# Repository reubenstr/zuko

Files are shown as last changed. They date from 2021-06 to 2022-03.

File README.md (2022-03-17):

# Zuko - A quadruped robot dog!

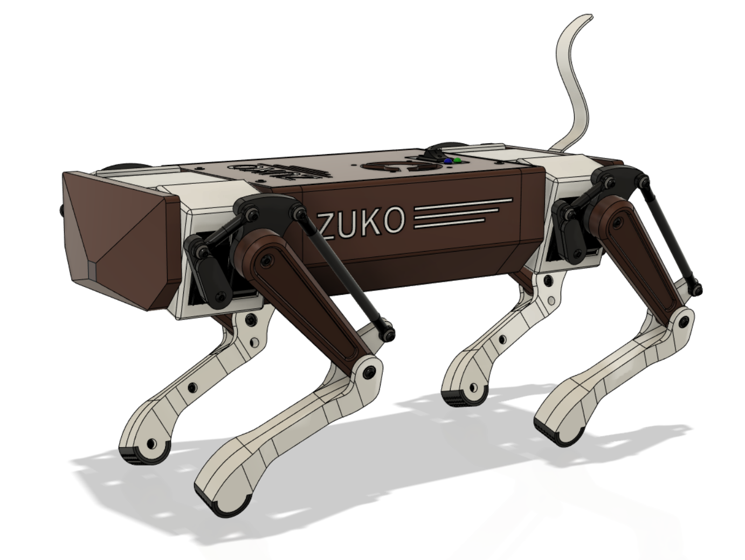
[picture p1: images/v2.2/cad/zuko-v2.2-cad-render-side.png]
 | 
------------ | 
Frame v2.2 CAD design. |

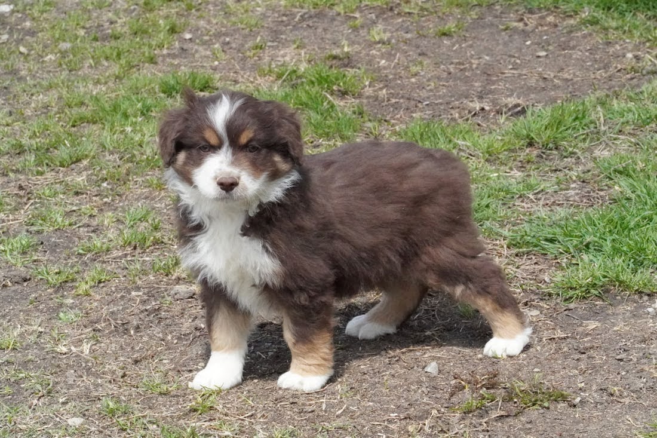
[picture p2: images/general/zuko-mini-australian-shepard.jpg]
 | 
------------ | 
Zuko himself! |

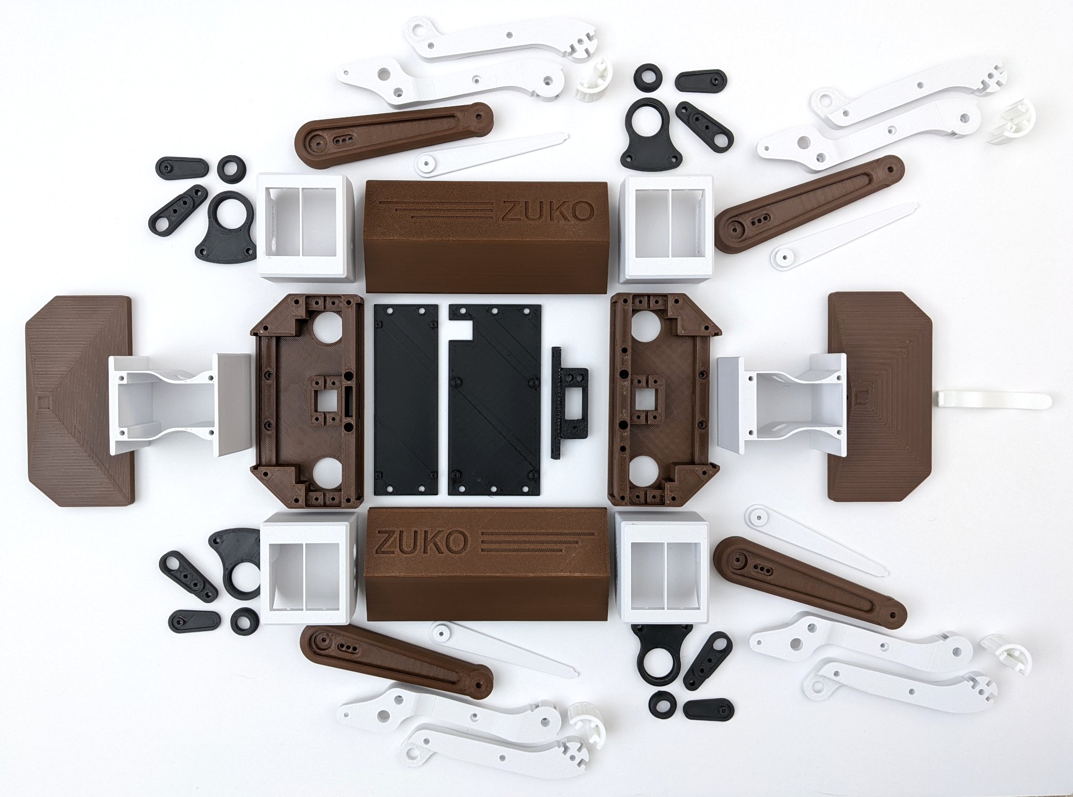
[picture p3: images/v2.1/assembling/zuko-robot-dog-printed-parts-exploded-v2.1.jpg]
 | 
------------ | 
Frame v2.1 parts printed. |

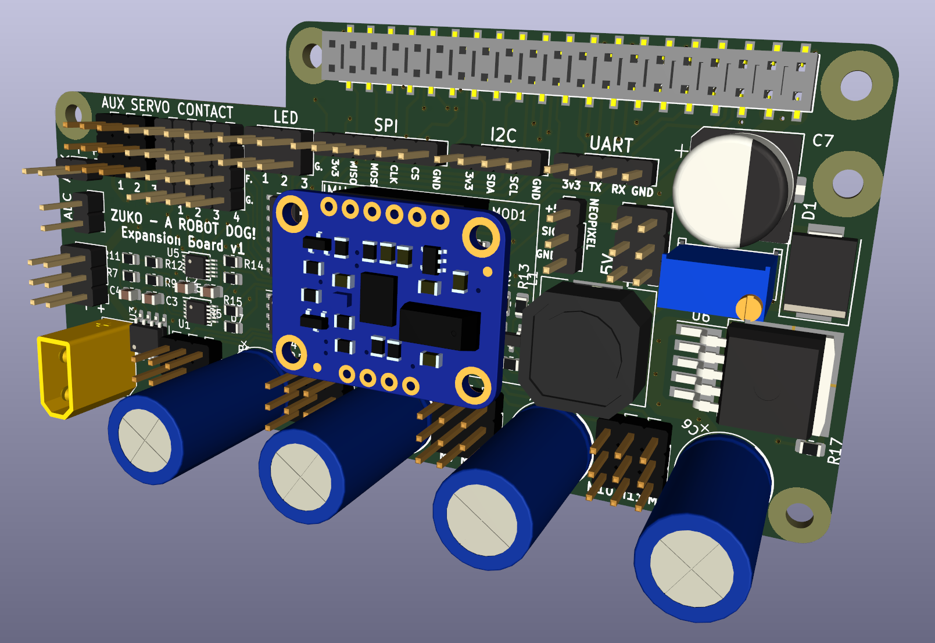
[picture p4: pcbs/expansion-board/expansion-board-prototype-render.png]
 | 
------------ | 
Expansion board v1 for direct RPi inteface. |

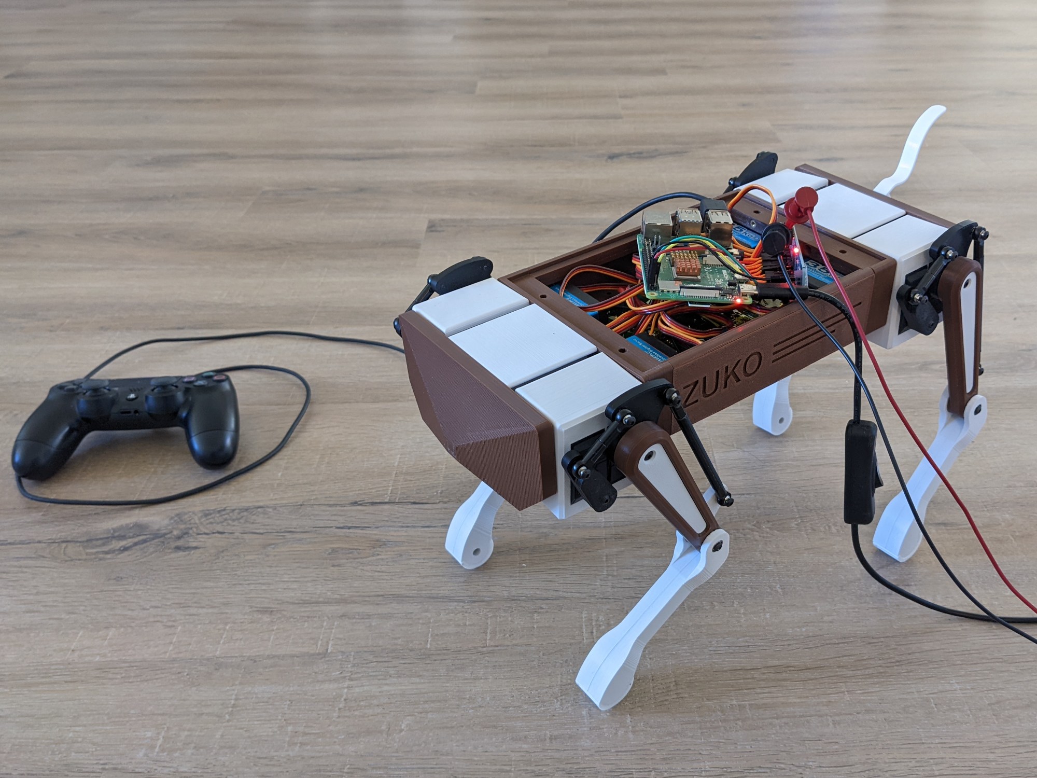
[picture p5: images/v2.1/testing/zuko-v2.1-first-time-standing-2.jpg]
 | 
------------ | 
Frame v2.1 first time standing. |

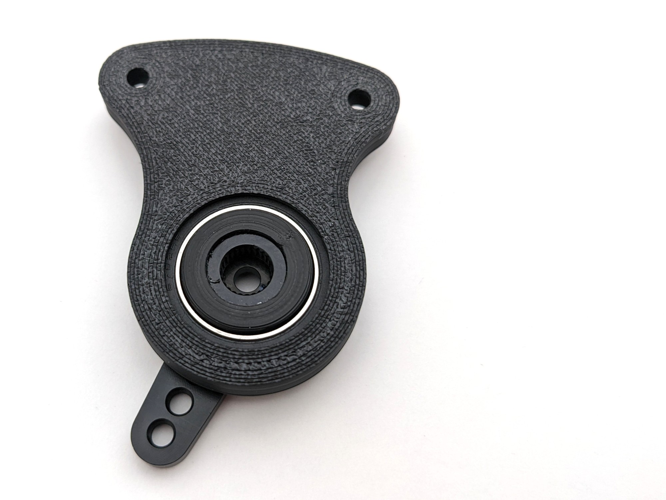
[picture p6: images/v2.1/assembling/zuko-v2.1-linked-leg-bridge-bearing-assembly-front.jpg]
 | 
------------ | 
Frame v2.1 upper leg's servo horn, linked leg bridge, and bridge bearing press fit together. |

Watch the video (https://youtu.be/D2snHtP22o0) | 
------------ | 
Video: frame v2.1 first tests |

Watch the video (https://youtu.be/J1g2Bx3SKjw) | 
------------ | 
Video: Sydney meets Zuko |

### Status

**Development.**  

**V2.2 Frame is being tested and is nearly ready for replication**

### General

Zuko uses the ROS2 framework for communication, launching, and 3rd party addons. Zuko uses a Rasberry Pi 4 with a custom expansion board for motor and peripheral control via a Playstation 4 controller.

### Current Major Tasks 

- Complete ROS2 tasks - in progress
- Fab/test expansion-board PCB
- Update BOM
- Create PCB BOM
- Upload STL's
- Create print time/weight sheet
- Create how to documentation for end user

### ROS2 Workspace 

ROS2 source code is contained the quad_ws directory.

### My contributions
- Frame redesign using larger servos, providing more space for electronics, rework of the leg/hip system, and addition of aesthetic features (tail, etc).
- Migration of source code from ROS1 to ROS2 (Robot Operating System) frameworks.
- Inverse kinematics for a linked leg system for OpenQuadruped / Spot Mini Mini based quadrupeds.
- Parameterized duplicated hard-coded values.
- Created servo calibration script for quicker calibration and servo support.- 
- A more feature rich motor and peripheral expansion board using a Teensy 4.0 supporting aux servos, foot sensors, NeoPixls, etc.
- 8x 18650 user accessable battery holder with onboard BMS (battery management system). 
  
### Credits
- Simulation, kinematics, bezier curves, and machine learning are largely based on the work from Spot Mini Mini: https://github.com/OpenQuadruped/spot_mini_mini 
- Spot Mini Mini is based on SpotMicroAI: https://spotmicroai.readthedocs.io/en/latest/
- Frame and leg linkage design inspired by Baris Alp's Kangel robot dog: https://grabcad.com/library/diy-quadruped-robot-1

### Communities
- SpotMicroAI Discord: https://discord.gg/m5fsENhT
- Quadrupedalism: https://quadrupedalism.com/

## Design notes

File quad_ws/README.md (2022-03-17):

# rpi_quad_ws
RPi 4 ROS2 workspace Zuko.

### Status

Development.

### Immediate To Do

- Update motor limits
- Finish URDF: add final STLs, add weights
- Add discovery to launch for remote simulation from RPi
- Update walking parameters
- Code in IMU, V/I sense, LEDs
- Pythonize code (clean up code)
- (clean model.py, urdf pathing)

### Long Term To Do

- Reconnect machine learning for better terrain navigation
- Update URDF for Gazebo
- Add speakers for barks
- Add camera for CV

### Notes

View documentation in the dev-notes folder

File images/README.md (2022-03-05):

# Zuko - images

When assembling check the latest CAD model as some pictures may show parts from past versions. 

Previous version pictures may be applicable to the current version, explore everything!

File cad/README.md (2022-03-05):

# Frame Versions

Select the latest version if you intend to make or redesign your own robot dog.

See the STL folder for assembly tools.

### v2.2 Change Log

	Removed TPU feet.
		Reduces filament types and lowers cost.
	Added EVA tape feet.
		Inceases grip.
	Lower legs redesigend to accommodate EVA tape feet.
	Added EVA tape feet glueing jig.

### v2.1 Change Log

	25t spline to gear adapters replaced with common servo horn.
		Increases part accessibility and to reduce cost. Suggested by SnowGliderr.
	Upper leg, lower leg servo horn, and hips redesigned to accept new servo horn.
	Frame bridge added top/bottom flair outs for aesthetics.
	Single unit electronics mounting plate for expansion board mounting direct to RPi4.
	Minor tweaks applied during assembly.
	
### v2.0 Change Log

	Replaced hip drive belts with direct drive by relocating hip motors into the electronics bay.
	Updated front and back center frames to support direct drive.
	Lengthened frame sides to accommodate space requirements for direct drive.
	Revised frame bridge from two peices into one to accommodate the removal of the hip servos. 
	Added ring bearing to upper leg and leg linkage bridge.
	Converted upper leg into two components, upper leg and gear interface, to accommodate the ring bearing's press fit joint.
	Revised hip joint pulley to accommodate direct drive.
	Added more support to the hip pulley connection area.
	Added more material support around lower leg linkage connection point.
	Revised lower leg to include a flair at the paw area.
	Removed brass insert requirement from hips, now using course threaded screws.
	Relocated power switch with stury direct frame connection.

	Results: 
		Pros:
			Fewer 3D printed parts, filament types, and hardware.
			No friction bearings.
			No stretchy hip angles.
			No leg assembly bridge wobble.
		Cons:			
			5mm longer frame resulting electronics bay space reduction (but electronics able to be housed in frame bridge)

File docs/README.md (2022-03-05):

# Docs

Documentation is currently being updated to reflect frame v2.2, the new RPi expansion board, and the updated ROS2 workspace quad_ws.

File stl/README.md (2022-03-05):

# STL

The main assembly archive located in the CAD folder will always contain the most up to date STL's.

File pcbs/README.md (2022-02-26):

# PCBs
 
PCBs created in KiCad 6.0

https://www.kicad.org/download/

All works in progress, PCBs on the way for testing, not for production.

There are currently two paths for controlling the servos and peripherals:

1) Expansion board: RPi 4 direct connect using PWM and ADC controllers of I2C
	
2) Motor Controller: Teensy is responsible for PWM and ADC at the expense of complex micro-ros.

### Expansion Board

RPi expansion board to control servo motors and other peripherals without using a microcontroller.

Fabrication specifications: 4 layer, 1oz (2oz preferred and may be required, testing still in progress).

### Battery Board

Mounts 8x 18650 LiPo batteries and 4x HY2120 (or similar) battery managment systems.

Fabrication specifications: 2 layer, 1oz (2oz preferred and may be required, testing still in progress).

### Motor Controller

Controls 12 motion RC servos using a Teensy 4.0 microcontroller. 

Connects to and powers RPi.

Requires external DC-DC converter to supply 5vDC to board and RPi.

Contains peripheral support for I2C IMU, touch down switches, LED, Neopixel (ws2812b) led strips, current sense, voltage sense, auxillary RC servos, and extra I2C devices.

Fabrication specifications: 4 layer, 1oz (2oz preferred and may be required, testing still in progress).

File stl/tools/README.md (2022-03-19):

# STL

Tools used to aid in the assembly and fabrication of Zuko.

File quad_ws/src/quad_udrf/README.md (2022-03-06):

# quad_udrf

Work in progress.

Zuko's URDF package. Uses xacro to create UDRF files. Visualized in RVIZ.

Launch UDRF in RVIZ:
	ros2 launch quad_urdf display.launch.py

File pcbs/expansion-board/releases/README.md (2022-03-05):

# Expansion Board Versions

v1.0: initial prototype for physical fabrication

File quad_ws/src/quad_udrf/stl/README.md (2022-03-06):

# stl
STL's are optimized for visualization and simulation with low vertice counts. Find 3D print ready STL's in the main project repository either from the archived CAD model or the STL folder.

To update STL's from main CAD model, export meshes with the following parameters (using Fusion 360):
	Format: STL (Binary)
	Unit Type: Meter
	Refinement: Low
	 
Use Fusion 360 to determine the STL's origin to perform joint offset calculations.

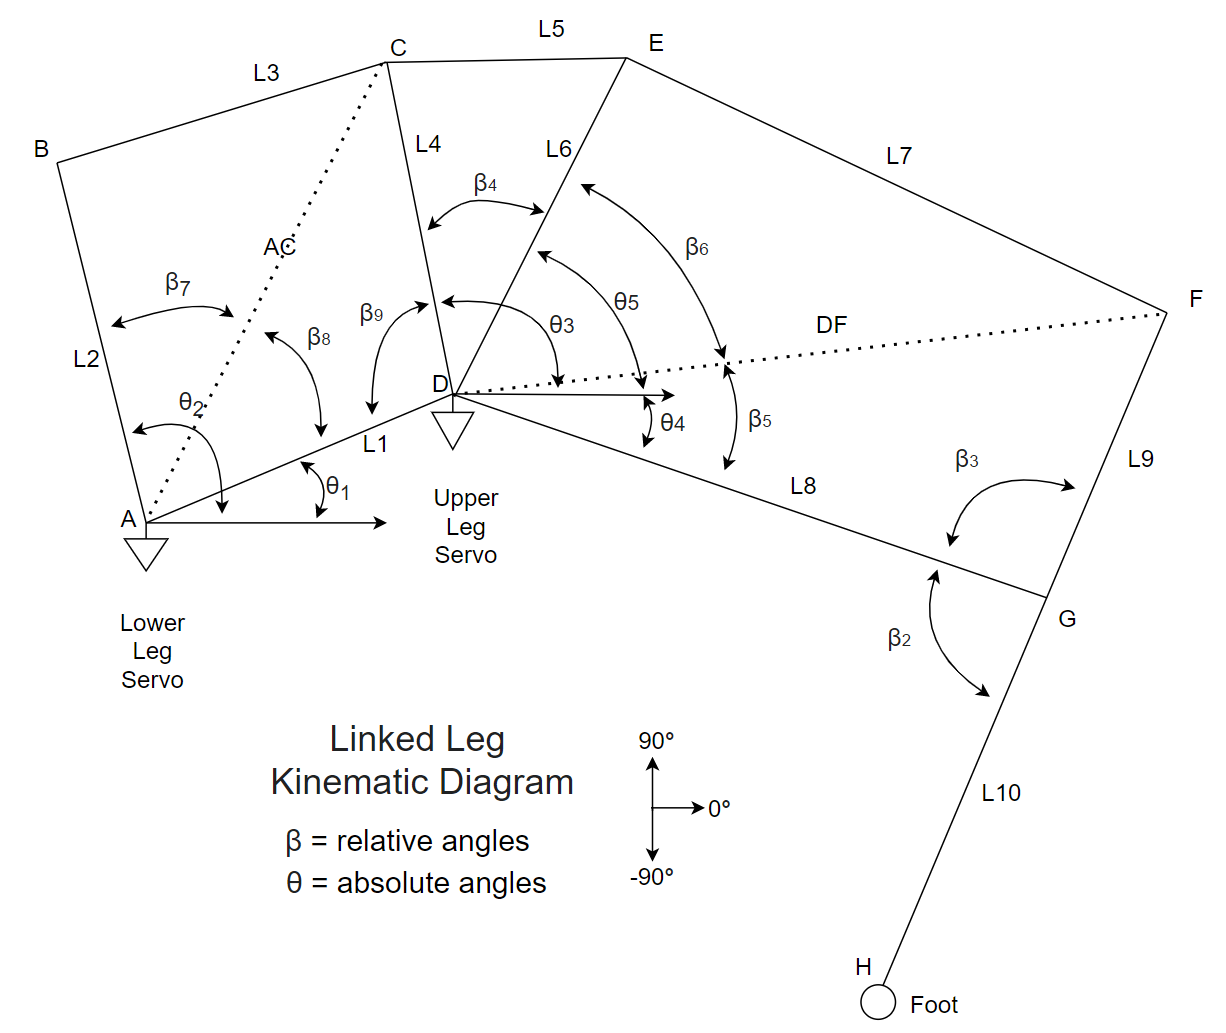
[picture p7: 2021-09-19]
diagrams/linked-leg-kinematic-dragram.png

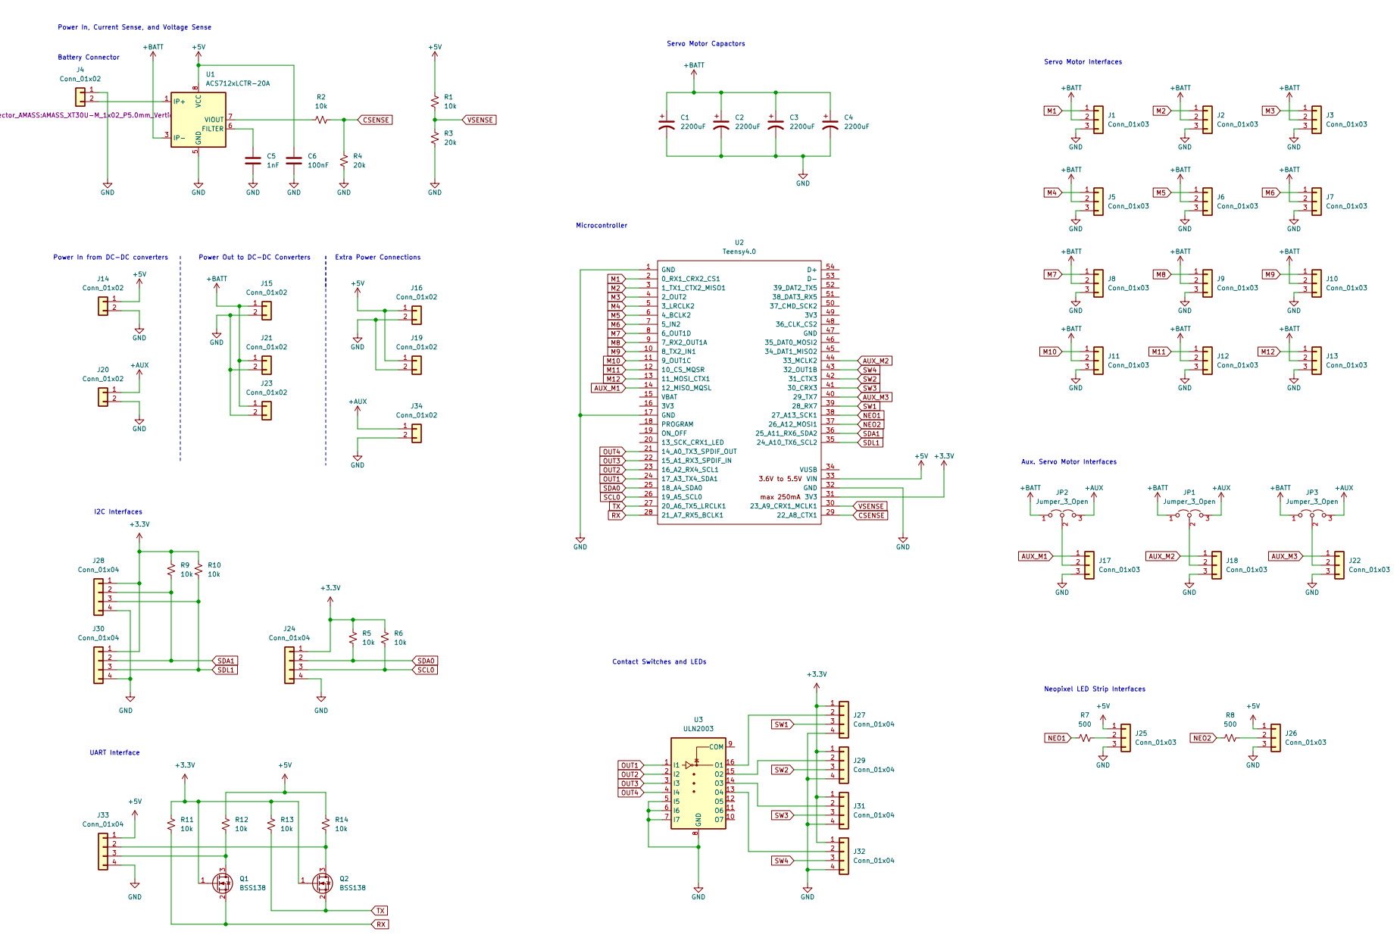
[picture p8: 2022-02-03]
pcbs/motor-controller/pcb-review-temp/pcb-schematic.png

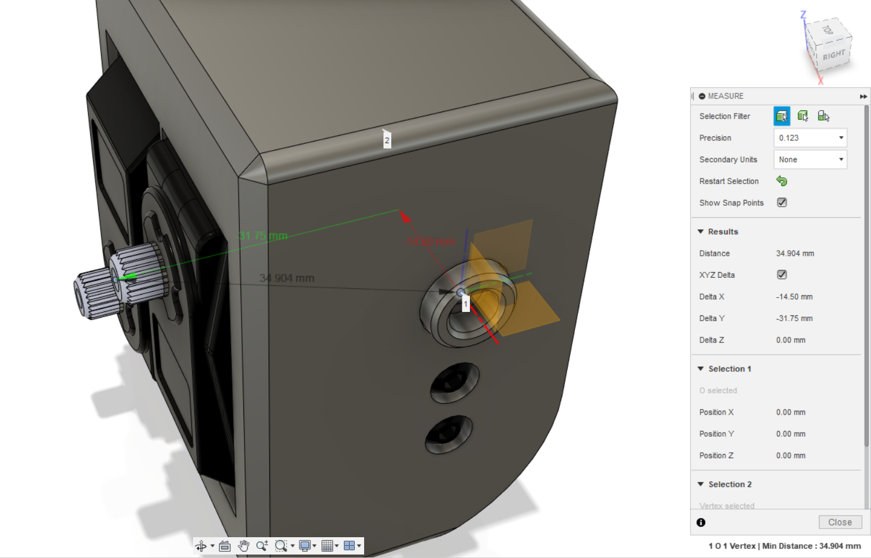
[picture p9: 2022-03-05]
images/general/zuko-showing-XYZ-delta-measuring-for-URDF-creation.png

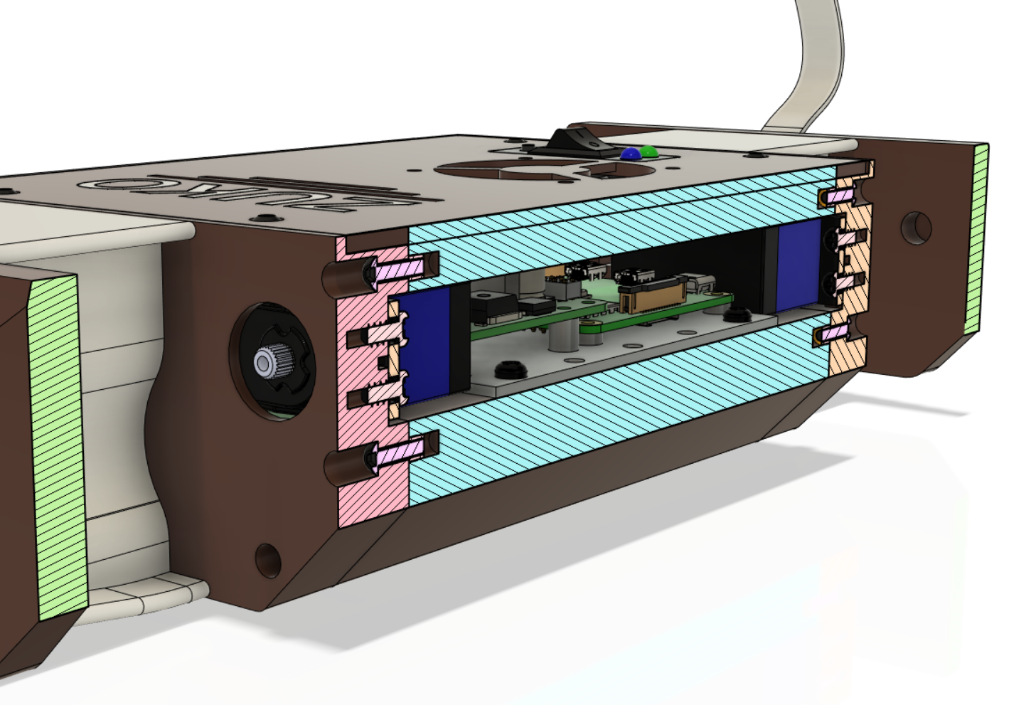
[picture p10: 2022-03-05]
images/v2.2/cad/zuko-v2.2-cad-render-side-cross-section.png

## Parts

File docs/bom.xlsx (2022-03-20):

Not fully updated for v2.2, check the CAD as it has most hardware
Links provided as examples.
Hardware | Qty. | Usages/Notes | Link1 | Link2
M3x3mm button head bolt | 8 | hip servo horn
M3x6mm button head bolt | 20 | PCB mounting plates, battery board, lower leg servo horn
M3x8mm button head bolt | 24 | combine lower legs, electronics bay cover, tail, hip bearing, power switch bracket, battery cover, lower leg bearing, front/back plate mount to sides
M3x12mm button head bolt | 32 | lower leg servo horn, lower leg tie rods
M3x16mm button head bolt | 8 | upper leg servo, lower leg feet
M3x65mm socket head bolt | 8 | center frames to bridge to face/butt
M4x8mm course thread self-tapping for plastic screw | 52
M2.3x6mm screw | 6 | RPi and expansion-board PCB mount
15mm x 21mm x 4mm, 6702-2RS bearing | 4 | Upper leg and lower leg bridge interface
8mm x 3mm x 4mm, 693ZZ bearing | 12 | hips, lower leg
M3x4.0mm, OD4.6mm threaded insert | TBD
M3x90mm threaded rod | 4 | lower leg tie rod
M3x16mm threaded rod | 4 | lower leg tie rod
M3 metal ball end tie rods | 16 |  | https://www.amazon.com/gp/product/B07FD4SMQJ
25T, 28.5mm length, 3x M3 holes servo horn | 12 |  | https://www.aliexpress.com/item/1005001513123335.html | https://www.amazon.com/gp/product/B09JLLWDW2
Mechatronics | Qty. | Usages/Notes | Link1 | Link2
35kg DSSERVO 180-degree servo | 12 | Testing on this specific servo is still being performed Many other high voltage high torque servos exists. | https://www.aliexpress.com/item/33010787343.html
Electronics | Qty. | Usages/Notes | Link1 | Link2
Rocker switch | 1
XT30 male | 1
XT30 Female | 1
Tactile switch | 1
5mm LED blue | 1
5mm LED red | 1
16AWG silicon multi-stranded
Heat shrink tubing
RPi 4
Rpi 4 expansion-board PCB |  |  | See git repository for expansion-board KiCAD project
Expansion-board components |  | TODO, check the schematic meanwhile | See git repository for expansion-board KiCAD project
Battery holder PCB | 1 | TODO, check the schematic meanwhile | See git repository for battery-holder KiCAD project
Li-ion lithium battery 18650 protection board | 4 |  | https://www.amazon.com/gp/product/B08CV2VS8G
18650 battery holder 4x cell capacity | 2 |  | https://www.amazon.com/gp/product/B07PZKKZY2
18650 battery | 8 | Use trusted retailer to buy quality batteries
Kapton tape (polyimide) |  | Covers battery board to protect against shorts | https://www.amazon.com/dp/B072Z92QZ2
18650 battery charger | 1
Playstation 4 wireless controller | 1 | Code modification required for other controllers | https://www.amazon.com/dp/B07VBBJ6KZ
Consumables | Qty. | Usages/Notes | Link1 | Link2
ABS 1.75mm filament – primary color | 1 | eSun Brown ABS – excellent filament | https://www.amazon.com/gp/product/B00MVIPTH8
ABS 1.75mm filament – secondary color | 1 | eSun White ABS – might be replaced as white has low strength | https://www.amazon.com/gp/product/B00MV7T3TO
ABS 1.75mm filament – tertiary color | 1 | eSun black ABS– try to find the ABS+ version, prints well, looks good | https://www.amazon.com/dp/B00MV7T25E/
TPU 1.75 filament – optional | 1 | Overture white TPU – optional for a tail | https://www.amazon.com/gp/product/B07VGVW546
EVA tape – bike handle bar tape |  | Or other grip tape/foam, ~2.50mm thick | https://www.amazon.com/dp/B07RDHK8TW
Solder
Solder flux
Superglue (cyanoacrylate) |  | attaches EVA tape to foot | https://www.amazon.com/s?k=super+glue
Threadlocker blue |  | keeps tie rod bolts from backing out | https://www.amazon.com/s?k=blue+threadlocker

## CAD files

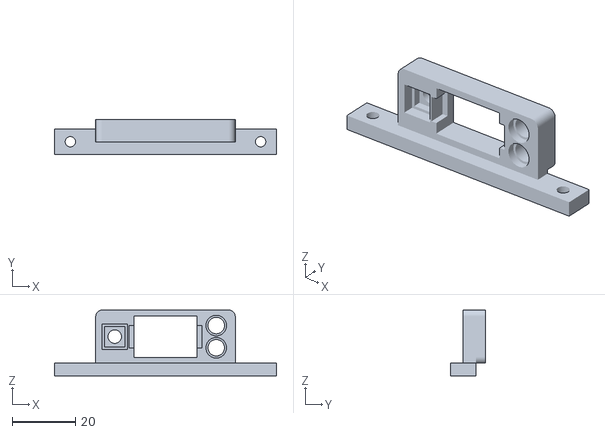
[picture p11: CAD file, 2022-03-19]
stl/v2.2/electronics - main switch mounting.stl
70.0 x 11.0 x 20.8

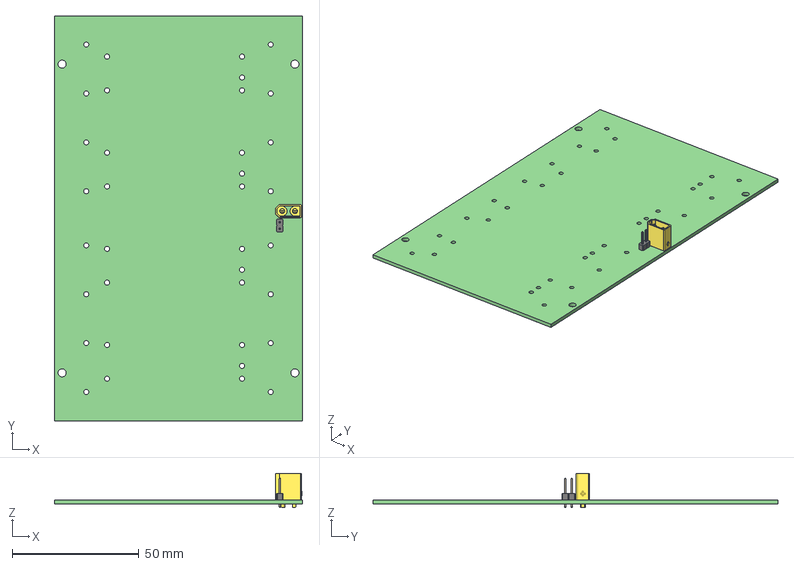
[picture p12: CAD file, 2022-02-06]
pcbs/battery-board/battery-board.step
98.0 x 160.0 x 13.5 mm
_autosave-battery-board PCB

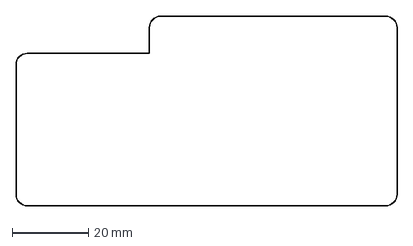
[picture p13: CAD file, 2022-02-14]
pcbs/expansion-board/expansion-board-pcb-outline.dxf
100.0 x 49.8 mm

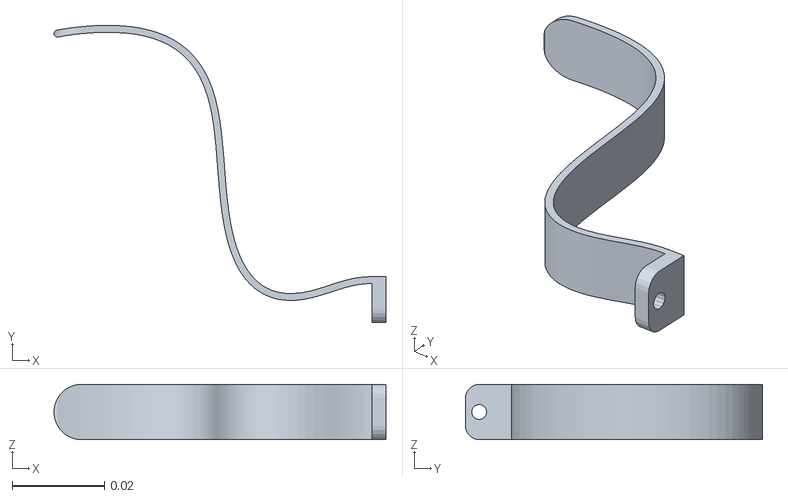
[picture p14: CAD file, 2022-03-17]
quad_ws/src/quad_simulation/quad_simulation/stl/tail.stl
0.072 x 0.0645 x 0.012

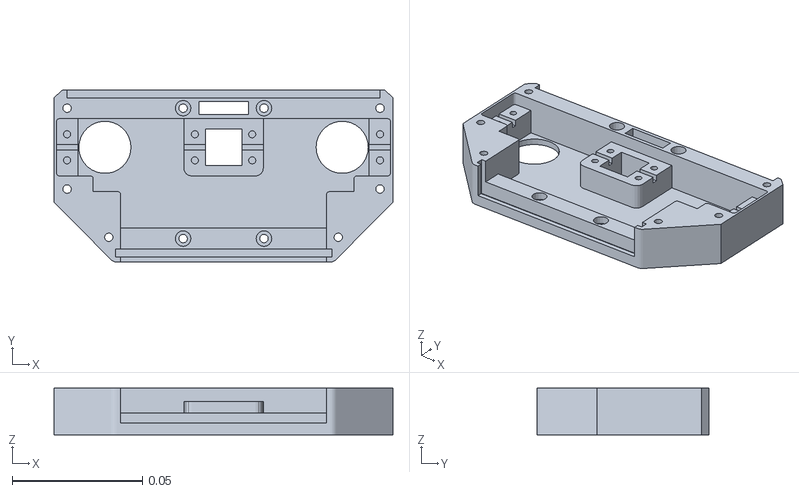
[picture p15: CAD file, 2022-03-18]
quad_ws/src/quad_udrf/stl/center_front.stl
0.13 x 0.066 x 0.018

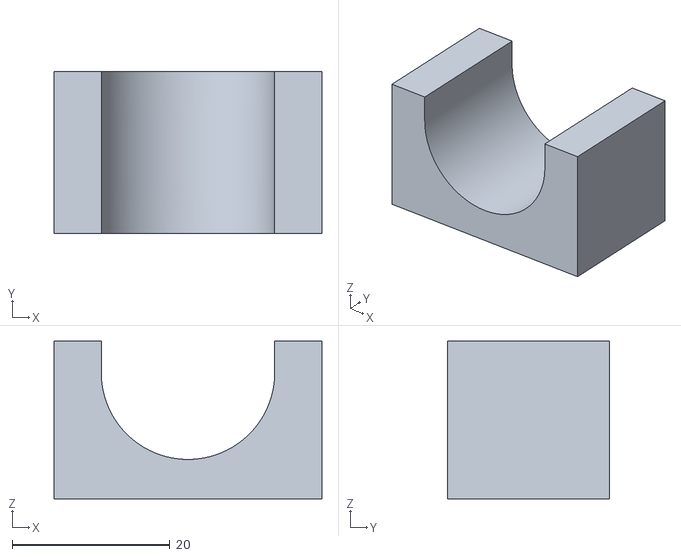
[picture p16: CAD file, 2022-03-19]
stl/tools/v2.2/tool - glue EVA tape to foot holder v2.stl
34.0 x 20.5 x 20.0

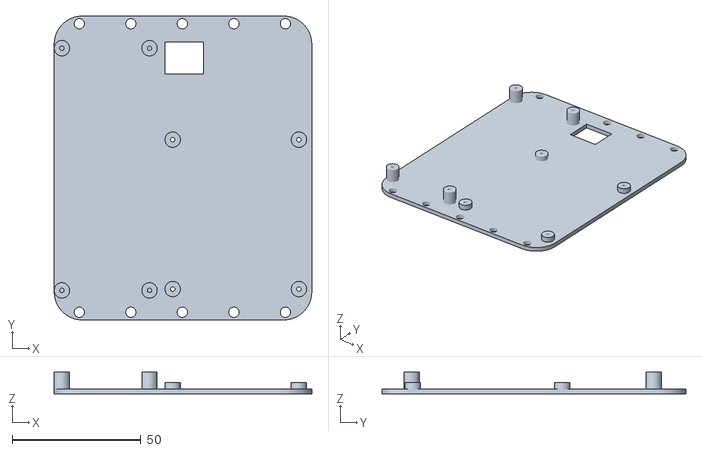
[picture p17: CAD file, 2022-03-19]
stl/v2.2/electronics - electronics mount.stl
100.0 x 118.0 x 8.50

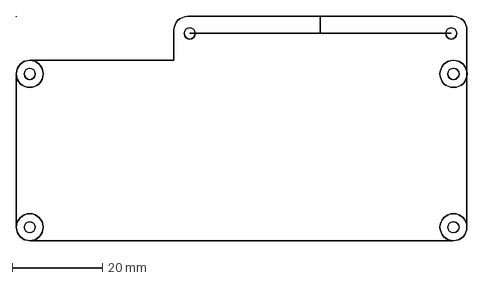
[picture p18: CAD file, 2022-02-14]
pcbs/expansion-board/expansion-board-user-guides.dxf
100.1 x 49.8 mm

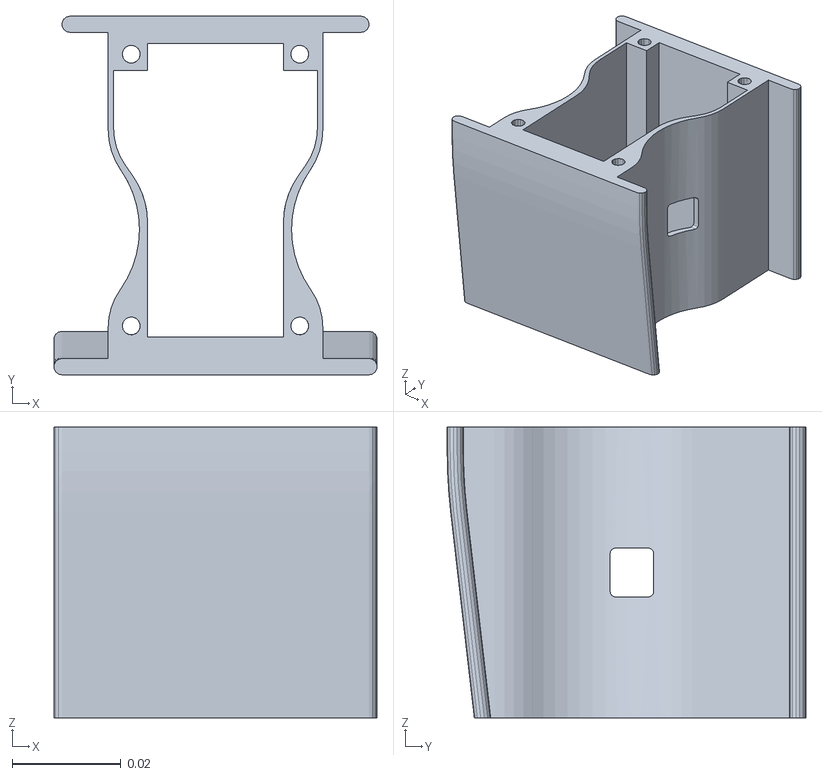
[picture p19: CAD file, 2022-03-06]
quad_ws/src/quad_simulation/quad_simulation/stl/bridge_front.stl
0.0594 x 0.066 x 0.0535

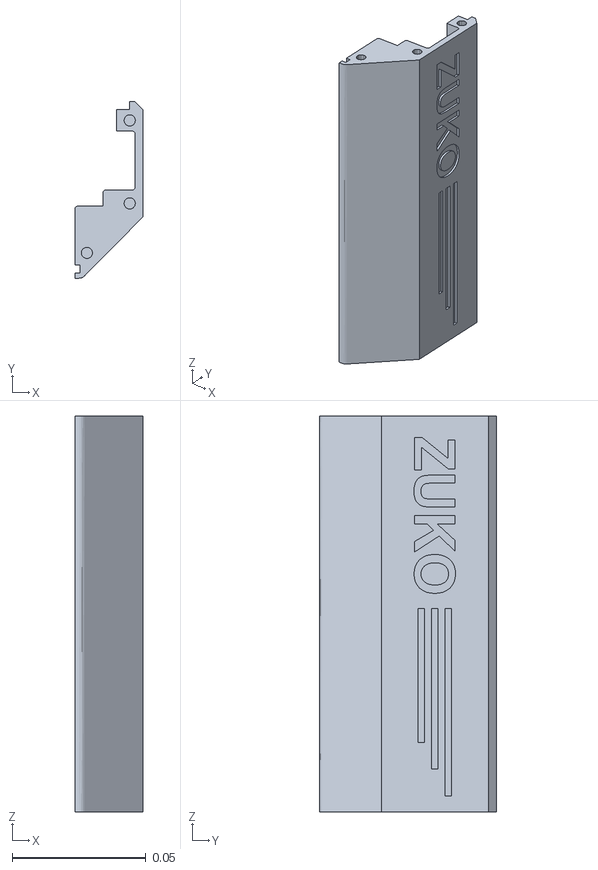
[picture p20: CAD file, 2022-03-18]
quad_ws/src/quad_udrf/stl/side_left.stl
0.0255 x 0.066 x 0.148

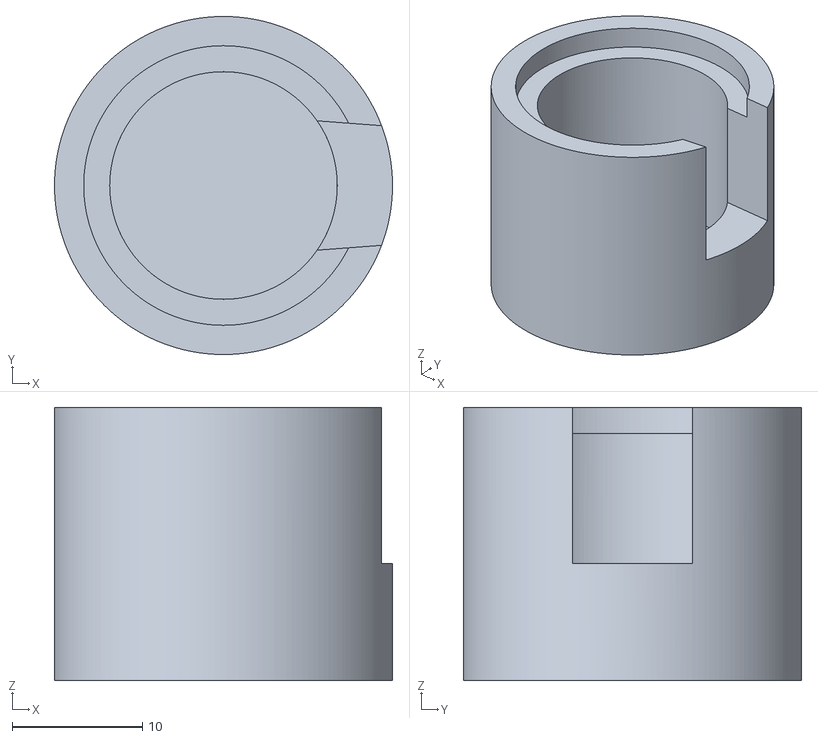
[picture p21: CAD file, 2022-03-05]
stl/tools/v2.2/tool - remove leg bearing from gear interface - hammer v8.stl
26.0 x 26.0 x 21.0

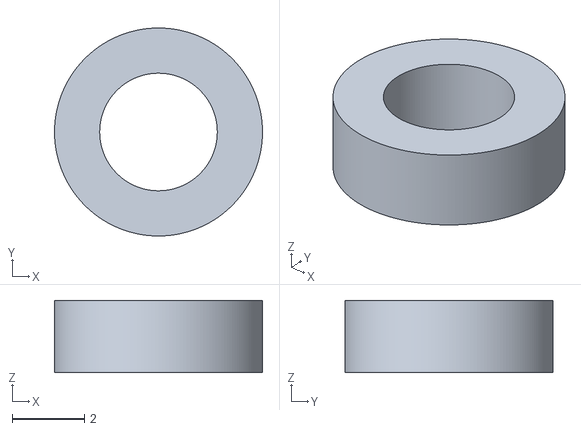
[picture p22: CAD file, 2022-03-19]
stl/v2.2/leg - upper - servo horn support ring.stl
5.75 x 5.75 x 2.00

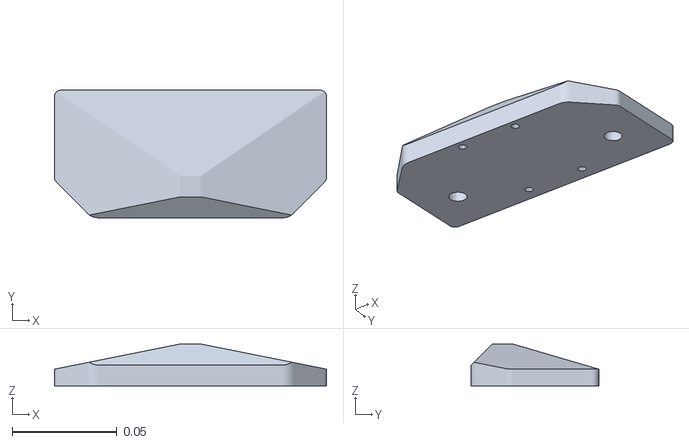
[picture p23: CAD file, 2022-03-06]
quad_ws/src/quad_simulation/quad_simulation/stl/face.stl
0.13 x 0.061 x 0.02

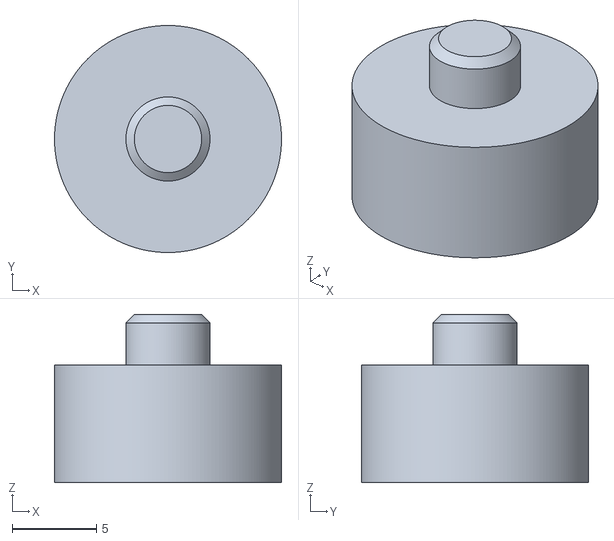
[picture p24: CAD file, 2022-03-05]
stl/tools/v2.2/tool - remove leg bearing from gear interface - base v6.stl
13.5 x 13.5 x 10.0

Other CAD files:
cad/v1.0/_ROBO_FRONT_FRAME.DXF
quad_ws/src/quad_udrf/stl/side_right.stl
stl/v2.2/electronics - battery cover.stl
quad_ws/src/quad_simulation/quad_simulation/stl/butt.stl
quad_ws/src/quad_simulation/quad_simulation/stl/bridge_back.stl
quad_ws/src/quad_simulation/quad_simulation/stl/center_back.stl
quad_ws/src/quad_simulation/quad_simulation/stl/center_front.stl
quad_ws/src/quad_simulation/quad_simulation/stl/hip_back.stl
quad_ws/src/quad_simulation/quad_simulation/stl/hip_front.stl
quad_ws/src/quad_simulation/quad_simulation/stl/lower_leg.stl
quad_ws/src/quad_simulation/quad_simulation/stl/side_left.stl
quad_ws/src/quad_simulation/quad_simulation/stl/side_right.stl
quad_ws/src/quad_simulation/quad_simulation/stl/upper_leg.stl
quad_ws/src/quad_udrf/stl/battery_cover.stl
quad_ws/src/quad_udrf/stl/bridge_back.stl
quad_ws/src/quad_udrf/stl/butt.stl
quad_ws/src/quad_udrf/stl/center_back.stl
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

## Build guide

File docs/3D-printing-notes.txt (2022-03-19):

3D PRINTING NOTES:

	Printing settings are tuned to the filament and printers used to create the orginal Zuko.
	Settings likley will need adjustment to match your filament, printers, ambient temperature, etc.
	Slicer configuration naming convention follows the Cura slicer nomenclature.
			
	Printers:
		Voron 2.4:
			Large parts
		Voron 0.1:
			Small parts
		
	Filaments:
		ABS:
			Black: 
				eSun ABS+
			Brown: 
				eSun ABS
			White: 
				eSun ABS		
		TPU (optional):
			White: 
				Overature TPU
		PLA (optional):
			Black: 
				Overture Matte Black PLA			
	
	Most parts should printed in ABS for heat resistance properties (direct sunlight). 
	Other materials such as ASA, carbon fiber, and polycarbonate should also work but are untested.
	Some parts may be printed in PLA for convenience such as electronic mounting plates.
			
	The upper leg bearing interface is a press fit, scaling trial and error is likely to acheive a tight press fit.
	
	TPU is optional if you want a tail as shown in the CAD model.
		
TIPS & TRICKS:
	Shrinking parts:
		ABS will shrink and parts likely will need to be scaled during slicing to match your brand of ABS.
	Prevent lifted corners:
		ABS must be printed in an enclosure free from air current, with a high bed temperature, and (in some cases) an enabled cooling fan.
	Smoother top layers for better fits:
		Top surface skin layers: 2
		Top surface skin flow: 90%
	Cleaner TPU surfaces:
		Reduce temperature.
	Adhesion:
		PEI build plates work very well.
		
PARTS:
	ABS BLACK:	
		Default settings:
			Layer height: 0.2mm
			Wall line count: 4
			Infill: 50%
			Printing temperature: 250c
			Build plate temperature: 110c
			Initial layer flow: 110%
			Print speed: 120mm/s
			Initial layer speed: 30mm/s		
			Cooling: enabled
			Fan speed: 25%	
		
		Link Bridge:	
			Scale: 100.6%
			Z-Seam alignment: Random (!important)
			
		Lower leg bearing press ring:
			Scale: 100.6%
			Z-Seam alignment: Random (!important)
			
		Upper leg - servo horn support ring:
			Scale: 100.6%

		Servo horn:
			Scale: 100.6%
			Generate support: enabled
			Support density: 50%
			
		Servo horn cover:			
			Scale: 100.8%
									
		Tie Rod Cover:
			Scale: 100%
			Print speed: 60mm/s
			Cooling: enabled			
			Build plate adhesion type: brim		
			
		Electronics - switch bracket:			
			Scale: 100.8%
			Generate support: enabled
			Support density: 20%	

		Tools (all):
			Scale: 100.8%
			Infill: 80%
			
		Foot:			
			Infill density: 80%
			Scale: 100.5%
			Cooling: Enabled
			Cooling Fan Speed: 50%
			Support: enabled
			Support density: 50%
		
	ABS BROWN:
		Default settings:
			Wall line count: 3
			Printing temperature: 250c
			Build plate temperature: 100c
			Print speed: 120mm/s			
			Layer height: 0.2mm	
			Cooling: disabled
			Infill: 20%
			Minimum Layer Time: 30s		
			Support: disabled
			
		Center Frame - Front, Back:
			Note:
				Corner lifting is very bad with this part, may require a well 
				sealed enclosure and extra build plate adhesion.
			Layer Height: 0.3mm				
			Support: enabled
			Support density: 50%
			Scale: 100.35%			
			
		Upper leg main body:				
			Infill density: 20%
			Cooling: enabled
			Fan speed: 40%			
			Support: enabled
			Support placement: touching buildplate
			Support density: 50%		
			
		Face plate, butt plate	
			Note:
				Cooling increased stop layer quality significantly.
			Layer height: 0.2mm
			Infill density: 10% 
			Cooling: enabled
			Fan speed: 40%
			Support: enabled
			Support density: 50%
			Scale: 100.35%		
			
		Sides	
			Layer Height: 0.3mm						
			Scale: 100.35%	
			
		Top cover, battery bay cover
			Print speed: 150mm/s
			Layer height: 0.3mm

	ABS WHITE: 	
		Default settings:
			Wall line count: 3
			Printing temperature: 250c
			Build plate temperature: 110c
			Infill: 20%
			Print Speed: 120mm/s
			Layer Height: 0.2mm	
			Cooling: disabled
			Support: disabled
		
		Lower leg - inner, outer:
			Print speed: 100mm/s
			Infill Density: 80%
			Scale: 100.35%
			Cooling: Enabled
			Cooling Fan Speed: 25%
			Support: enabled
			Support density: 50%
		Hip:
			Scale: 100.35%	
			Cooling fan: 25%
			Support: enabled
			
			Support structure: grid
			Support density: 60%
			- or -
			Support structure: Tree
			Support placement: Touching Buildplate
		
		Frame Bridge:	
			Scale: 100.35%	
			Layer Height: 0.3mm	
			Wall line count: 2
			Infill Density: 15%
			Cooling: Enabled
			Cooling Fan Speed: 25%		
				
	PLA:
		Default settings:
			Layer height: 0.2mm
			Infill density: 20%
			Print speed 150mm/s
			Cooling: 100%
				
		Electronics mounting plate:
			Default settings	

	TPU:
		Default settings:
			Layer height: 0.2mm
			Infill density: 20%
			Printing temperature: 225C
			Build plate temperature: 60C
			Print speed: 20mm/s
			Enable cooling: enabled
			Fan speed: 100%
			Generate support: enabled
			
		Tail:
			Default settings

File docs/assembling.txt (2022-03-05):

Assembling Guide.

	Work in progress.

Caution:
	Threadlock breaks down ABS, do not allow threadlock to contact ABS parts. 
	
General tips:
	Don't over tighten bolts.

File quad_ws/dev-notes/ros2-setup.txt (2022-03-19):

General instructions to setup Ubuntu, and ROS2 on Desktop and RPi.

Install Ubuntu 20.04.0x LTS and setup Wi-Fi:
	RPi:
		Use Raspberry Pi Imager to install Ubuntu 20.04.4 LTS Server 64-bit
		First time boot user/pass: ubuntu/ubuntu
		Change to ubuntu/password (or your preference)
	Desktop:
		https://ubuntu.com/download/desktop	
	Wi-Fi:		
		sudoedit /etc/netplan/50-cloud-init.yaml
			add Wi-Fi configuration, example (no tabs, two spaces, keep quotation marks):
				version: 2
				ethernets:
				eth0:
					dhcp4: true
					optional: true
				wifis:
				wlan0:
					dhcp4: true
					optional: true
					access-points:				
					lab-wifi-ssid:
						password: "password"
		sudo touch /etc/cloud/cloud.cfg.d/99-custom-networking.cfg
		sudoedit /etc/cloud/cloud.cfg.d/99-custom-networking.cfg	
			add the below line verbatim:
				network: {config: disabled}
		Apply netplan:
			sudo netplan apply
		Check for connection and IP address:
			ip a
Tip:
	Use Putty to SSH into RPi for copy/paste ability of commands.
	
Install ROS2 Foxy:
	RPi:
		https://roboticsbackend.com/install-ros2-on-raspberry-pi/
	Desktop:
		https://roboticsbackend.com/install-ros2-on-raspberry-pi/
		Instead of installing ros-base install the desktop version:		
			sudo apt install ros-foxy-desktop
	
Clone repository and build:
	RPi & Desktop:	  	
		git clone https://github.com/reubenstr/zuko
		cd zuko/quad_ws	
		source /opt/ros/foxy/setup.bash	
		colcon build
	
At every startup, soure ROS, CD into the workspace, and source the workspace automatically:
	RPi & Desktop:
		echo "source /opt/ros/foxy/setup.bash" >> ~/.bashrc
		echo "cd zuko/quad_ws" >> ~/.bashrc
		echo "source install/local_setup.bash" >> ~/.bashrc

RPi only:
	Install dependencies:
		pip install smbus2		
		TODO: add more dependencies!

	Grant access to I2C every startup:	
		echo "sudo chmod a+rw /dev/i2c-*" >> ~/.bashrc

	Install bluetooth for wireless game controller:
		$ sudo apt install pi-bluetooth
		$ sudo reboot	
		$ sudo bluetoothctl
		 
		In the bluetoothctl terminal, find the controller's MAC address:
			scan on		
			scan off
		You should see bluetooth devices, example: "[CHG] Controller 84:30:95:48:0F:3C Pairable: yes"			
		Place the controller in pairing mode:
			PS4: 
				press share and PS buttons, front led will flash
		Copy the controller's MAC address and enter the command (using your MAC address):
			connect 84:30:95:48:0F:3C
		PS4 controller LED should be solid blue when paired.
		Add the controller to the trusted list automatically connect:
			trust 84:30:95:48:0F:3C		
		List paired devices:
			bluetoothctl paired-devices
	
	Servo calibration (execute from the workspace directory):
		cd src/quad_motors/quad_motors/
		./servo_calibration.py

Desktop only:
	Install dependencies:		
		pip install gym
		pip install pybullet
		TODO: add more dependencies!

	Test the controller using jstest-gtk:
			sudo apt install jstest-gtk

RPi & Desktop:
	Launch:
		See ros-commands document to startup the robot.

Remote development in VSCode using SSH:
	In VSCode use Remote Viewer extenstion to edit RPi files remotely.
	Troubleshooting:
		Failed to connect (after reinstalling OS):
			Delete contents in host machine known_hosts file, example:
				C:\Users\DrZoidburg\.ssh\known_hosts

I2C:
	Tools:
		sudo apt-get install i2c-tools
	Scan for device addresses on bus:
		sudo i2cdetect -y 1
	Scan and dump registers on device:
		i2cdump -y 1 0x40

Misc:
	Show connect wireless controller info:
		cat /proc/bus/input/devices
		ls /dev/input/by-id/
		dmesg | grep input

	sudo apt install bluez-tools

	sudo apt install evtest

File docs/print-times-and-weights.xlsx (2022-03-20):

Estimated print material and time using printing parameters in 3D-pirinting-notes.txt
Times based on single part prints.
Frame v2.2
Part | Quantity | Mass (g) (w/support) | Time (m) | Total Mass | Total Time
electronics – batter cover | 1 | 32 | 87 | 32 | 87
electronics – electronics mount | 1 | 19 | 79 | 19 | 79
electronics – main switch mount | 1 | 5 | 29 | 5 | 29
foot | 4 | 2 | 16 | 8 | 64
frame - bridge - back | 1 | 35 | 122 | 35 | 122
frame - bridge - front | 1 | 39 | 123 | 39 | 123
frame - center - back | 1 | 43 | 139 | 43 | 139
frame - center - front | 1 | 44 | 142 | 44 | 142
frame - butt - plain | 1 | 36 | 132 | 36 | 132
frame - face - plain | 1 | 40 | 148 | 40 | 148
frame - side - left | 1 | 50 | 132 | 50 | 132
frame - side - right | 1 | 50 | 131 | 50 | 131
frame - top cover | 1 | 44 | 119 | 44 | 119
hip - servo mount | 4 | 22 | 99 | 88 | 396
hip - thrust washer - bearing side | 4
leg - bridge | 4 | 3 | 14 | 12 | 56
leg - lower - inner | 4 | 13 | 55 | 52 | 220
leg - lower - link cover | 4 | 2 | 29 | 8 | 116
leg - lower - outer | 4 | 10 | 46 | 40 | 184
leg - lower - servo bridge - bearing press ring | 4 | 1 | 7 | 4 | 28
leg - lower - servo horn – cover | 4 | 1 | 6 | 4 | 24
leg - lower - servo horn | 4 | 2 | 12 | 8 | 48
leg - upper - infill | 4 | 2 | 14 | 8 | 56
leg - upper - servo horn support ring | 4 | 1 | 1 | 4 | 4
leg - upper | 4 | 15 | 57 | 60 | 228
misc - tail | 1 | 3 | 57 | 3 | 57
 | Totals | 65 | Parts
 |  | 736 | Mass (grams)
 |  | 2864 | Print Time (minutes)
 |  | 47.7 | Print Time (hours)

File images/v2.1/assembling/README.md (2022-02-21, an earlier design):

# Zuko - frame v2.1

Some assembly pictures show the older battery board from frame v1.

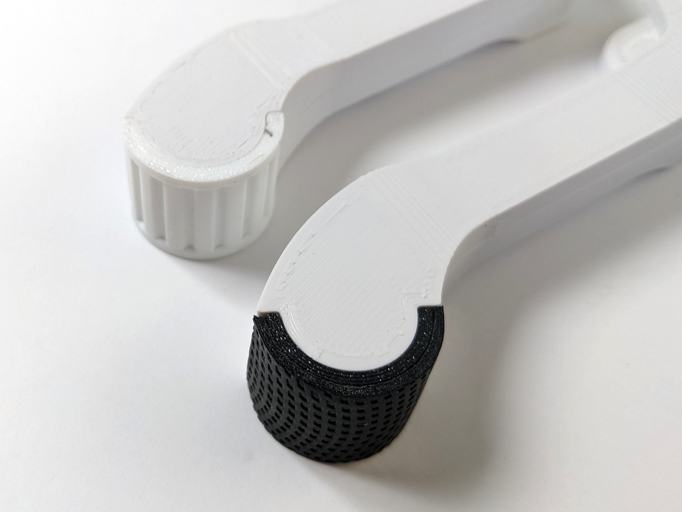
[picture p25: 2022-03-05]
images/v2.2/assembly/zuko-v2.2-foot-eva-tape-vs-tpu.jpg

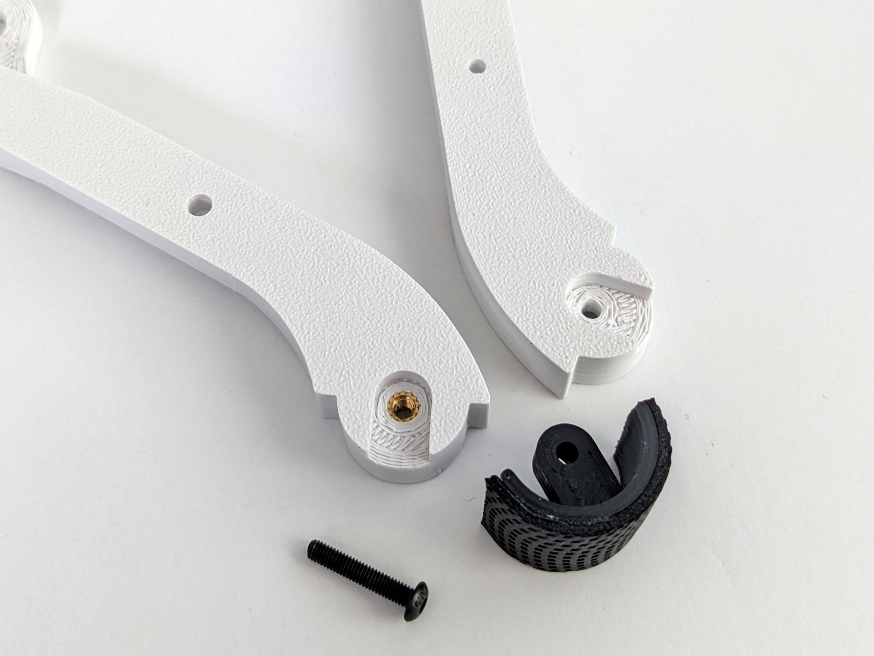
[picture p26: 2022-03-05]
images/v2.2/assembly/zuko-v2.2-foot-and-lower-leg.jpg

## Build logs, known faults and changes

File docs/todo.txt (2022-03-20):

###############################################################################

Immediate fixes, updates, actions:

	CAD Assembly:	
		add 50mm fan screws
		
	Reprint/Redesign:

	Battery Holder PCB:
		Increase mounting screw size to fit M4 course thread screws
		
	Documentation:
		electronics bom
	
###############################################################################	

Future improvements and other thoughts (for a later major revision, unplanned):
	Add battery charging capability without removing batteries
	Add contact sensors to feet
	Watch lower leg and hip bearings, might need to increase size
	Add integrated camera
	Add face
	Add ears
	Add barks (speaker and amplifier)
	Add top plate with mounting hole grid for equipment (lidar) tests

###############################################################################
		
Temp notes:
	Weight:
		frame w/electronics: 1895g
		batteries: 94g * 4 = 376g
		top/bottom cover : 76g
		fan: 12g
		+misc.: 50g
		=== ~2200g
		
###############################################################################

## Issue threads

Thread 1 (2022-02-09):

Accessibility regarding requirement of servo spline gear

SnowGliderr, 2022-02-09:
The servo spline gear (25T internal, 12T external) used in this design is patented as seen in
servocity.com/2305-series-brass-mod-0-8-servo-gear-25-tooth-spline-12-tooth. This significantly impacts its availability compared to the other parts of Zuko, that can mostly be sourced from a multitude of manufacturers or substituted with similar parts, despite being a relatively simple hardware component. For example, the more commonly used 20mm metal disc servo horn is available from many sites internationally for just a few dollars (or just a couple in some areas) for all 12. On the other hand, the servo spline gear appears to be almost non-existent outside of specialty stores, and even the relatively cheap Aliexpress link provided in the BOM puts them at about the cost the cost of about 2 high torque servos for the 12 pieces required. As such, it would be great if Zuko could officially be compatible with metal disc servo horns, or if the use of the spline gears were reduced. At least for the hip servos, it should be possible to use metal discs by lengthening the chassis slightly and widening a few holes.

P.S. Thanks for the great contributions in porting OpenQuad code to ROS 2 and a Kangal-style chassis.

reubenstr, 2022-02-10:
Completely agree on all points. With this, I am reworking all joints to accept a more commonly available servo horn. The following image/URLs are to a horn that has enough shaft length to allow the upper leg joint to retain the ability to support the lower leg's linking bridge' press bearing needed for smooth motion:
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
https://www.amazon.com/gp/product/B09JLLWDW2
https://www.aliexpress.com/item/1005001513123335.html

Here are screenshots of the upper leg rework and the hip  preliminary reworked joints:

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

So far I don't foresee any diminished aesthetics or reduced mechanical rigidity. There is slightly added difficulty in printing the hip module, but should be negligible.

Thanks for the feedback! I will close the issue after test prints work out. Please let me know your opinion of this solution.

.

SnowGliderr, 2022-02-10:
This looks like an elegant solution for the hips and upper legs, and the horns are easier to source. Seems like the rod end links will need to be shifted outwards to accommodate the thickness of the horn for the lower leg servo.

reubenstr, 2022-02-13:
Redesign complete.

An adapter was created for the lower leg drive horn to keep the linkages as close to the driving servo as the original design.

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

Printed parts are working well, likely minor tweaks for the press fit of the leg bearing as I begin to assemble the new parts.

Closed 2022-02-13.

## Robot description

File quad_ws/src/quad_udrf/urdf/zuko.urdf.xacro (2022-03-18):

<?xml version="1.0"?>
<robot name="zuko" xmlns:xacro="http://www.ros.org/wiki/xacro">

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
 
<xacro:macro name="mesh_link" params="name origin_xyz origin_rpy meshfile meshscale c_xyz matname mass i_xyz i_rpy length width height">
	<link name="${name}">
	  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

	  <inertial>
		<mass value="${mass}" />
		<origin rpy="${i_rpy}" xyz="${i_xyz}" /> 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
	  </inertial>
	</link>
	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
</xacro:macro>
  
<xacro:macro name="frame_joint" params="name type origin_rpy origin_xyz parent child">
	<joint name="${name}" type="${type}">
	  <origin rpy="${origin_rpy}" xyz="${origin_xyz}" />
	  <parent link="${parent}" />
	  <child link="${child}" />
	</joint>
</xacro:macro>

<xacro:macro name="rev_joint" params="name type axis_xyz origin_rpy origin_xyz parent child effort velocity damping friction upper lower">
    <joint name="${name}" type="${type}">
      <axis xyz="${axis_xyz}" />
      <origin rpy="${origin_rpy}" xyz="${origin_xyz}" />
      <parent link="${parent}" />
      <child link="${child}" />
      <limit effort="${effort}" velocity="${velocity}" lower="${lower}" upper="${upper}"/>
      <joint_properties damping="${damping}" friction="${friction}" />
    </joint>
  </xacro:macro>
  
<xacro:macro name="transmission" params="leg ">
    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
</xacro:macro>
  

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	
	<xacro:property name="center_thickness" value="0.018" />
	<xacro:property name="side_length" value="0.148" />
	<xacro:property name="bridge_length" value="0.0535" />
	<xacro:property name="center_origin_to_top_cover_inset" value="0.019" /> 

	<xacro:mesh_link name="base_link" origin_rpy="${pi/2} 0 -${pi/2}" origin_xyz="0 0 0" i_rpy="0 0 0" i_xyz="0 0 0" mass="0.6" c_xyz="0 0 0" length="0" width="0" height="0" matname="brown" meshfile="package://quad_urdf/stl/center_front.stl" meshscale="1 1 1" />

	<xacro:mesh_link name="side_left_link" origin_rpy="${pi/2} 0 ${pi/2}" origin_xyz="0 0 0" i_rpy="0 0 0" i_xyz="0 0 0" mass="0.6" c_xyz="0 0 0" length="0" width="0" height="0" matname="brown" meshfile="package://quad_urdf/stl/side_left.stl" meshscale="1 1 1" />
		
	<xacro:mesh_link name="side_right_link" origin_rpy="${pi/2} 0 -${pi/2}" origin_xyz="0 0 0" i_rpy="0 0 0" i_xyz="0 0 0" mass="0.6" c_xyz="0 0 0" length="0" width="0" height="0" matname="brown" meshfile="package://quad_urdf/stl/side_right.stl" meshscale="1 1 1" />
		
	<xacro:mesh_link name="center_back_link" origin_rpy="${pi/2} 0 ${pi/2}" origin_xyz="0 0 0" i_rpy="0 0 0" i_xyz="0 0 0" mass="0.6" c_xyz="0 0 0" length="0" width="0" height="0" matname="brown" meshfile="package://quad_urdf/stl/center_back.stl" meshscale="1 1 1" />
	
	<xacro:mesh_link name="bridge_front_link" origin_rpy="${pi/2} 0 -${pi/2}" origin_xyz="0 0 0" i_rpy="0 0 0" i_xyz="0 0 0" mass="0.6" c_xyz="0 0 0" length="0" width="0" height="0" matname="white" meshfile="package://quad_urdf/stl/bridge_front.stl" meshscale="1 1 1" />
		
			
	<xacro:mesh_link name="bridge_back_link" origin_rpy="${pi/2} 0 -${pi/2}" origin_xyz="0 0 0" i_rpy="0 0 0" i_xyz="0 0 0" mass="0.6" c_xyz="0 0 0" length="0" width="0" height="0" matname="white" meshfile="package://quad_urdf/stl/bridge_back.stl" meshscale="1 1 1" />
		
	<xacro:mesh_link name="face_link" origin_rpy="${pi/2} 0 ${pi/2}" origin_xyz="0 0 0" i_rpy="0 0 0" i_xyz="0 0 0" mass="0.6" c_xyz="0 0 0" length="0" width="0" height="0" matname="brown" meshfile="package://quad_urdf/stl/face.stl" meshscale="1 1 1" />
		
	<xacro:mesh_link name="butt_link" origin_rpy="${pi/2} 0 -${pi/2}" origin_xyz="0 0 0" i_rpy="0 0 0" i_xyz="0 0 0" mass="0.6" c_xyz="0 0 0" length="0" width="0" height="0" matname="brown" meshfile="package://quad_urdf/stl/butt.stl" meshscale="1 1 1" />

	<xacro:mesh_link name="electronics_cover_link" origin_rpy="0 0 0" origin_xyz="0 0 0" i_rpy="0 0 0" i_xyz="0 0 0" mass="0.6" c_xyz="0 0 0" length="0" width="0" height="0" matname="brown" meshfile="package://quad_urdf/stl/electronics_cover.stl" meshscale="1 1 1" />

	<xacro:mesh_link name="battery_cover_link" origin_rpy="0 0 0" origin_xyz="0 0 0" i_rpy="0 0 0" i_xyz="0 0 0" mass="0.6" c_xyz="0 0 0" length="0" width="0" height="0" matname="brown" meshfile="package://quad_urdf/stl/battery_cover.stl" meshscale="1 1 1" />

	<xacro:mesh_link name="tail_link" origin_rpy="${pi/2} ${35 * pi/180} 0" origin_xyz="0 0 0" i_rpy="0 0 0" i_xyz="0 0 0" mass="0.6" c_xyz="0 0 0" length="0" width="0" height="0" matname="white" meshfile="package://quad_urdf/stl/tail.stl" meshscale="1 1 1" />
		
		

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

<xacro:frame_joint name="side_left_joint" type="fixed" origin_rpy="0 0 0" origin_xyz="${-center_thickness - side_length} 0.060 0.015" parent="base_link" child="side_left_link"/>

<xacro:frame_joint name="side_right_joint" type="fixed" origin_rpy="0 0 0" origin_xyz="-${center_thickness} -0.060 0.015" parent="base_link" child="side_right_link"/>

<xacro:frame_joint name="center_back_joint" type="fixed" origin_rpy="0 0 0" origin_xyz="${-side_length - center_thickness - center_thickness} 0 0" parent="base_link" child="center_back_link"/>
			
<xacro:frame_joint name="bridge_front_joint" type="fixed" origin_rpy="0 0 0" origin_xyz="${bridge_length} 0 -0.010" parent="base_link" child="bridge_front_link"/>
  
<xacro:frame_joint name="bridge_back_joint" type="fixed" origin_rpy="0 0 0" origin_xyz="0 0 -0.010" parent="center_back_link" child="bridge_back_link"/>
			
<xacro:frame_joint name="face_joint" type="fixed" origin_rpy="0 0 0" origin_xyz="0 0 0" parent="bridge_front_link" child="face_link"/>
  
<xacro:frame_joint name="butt_joint" type="fixed" origin_rpy="0 0 0" origin_xyz="-${bridge_length} 0 0" parent="bridge_back_link" child="butt_link"/>  

<xacro:frame_joint name="electronics_cover_joint" type="fixed" origin_rpy="0 0 ${pi}" origin_xyz="${-0.089 - 0.003} 0 ${center_origin_to_top_cover_inset}" parent="base_link" child="electronics_cover_link"/>
  
<xacro:frame_joint name="battery_cover_joint" type="fixed" origin_rpy="${pi} 0 ${pi}" origin_xyz="${-0.09075 - 0.003} 0 -0.039" parent="base_link" child="battery_cover_link"/>  
						
<xacro:frame_joint name="tail_joint" type="fixed" origin_rpy="0 0 0 " origin_xyz="-0.012419 0 0.025687" parent="butt_link" child="tail_link"/>  


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		
		<xacro:property name="servo_flange_protrusion_from_center_distance" value="0.002" /> 
		<xacro:property name="hip_origin_to_upper_leg_servo_origin_x" value="${-0.0145}" /> 
		<xacro:property name="hip_origin_to_upper_leg_servo_origin_back_x" value="${-0.0145 - .021}" /> 	
		<xacro:property name="hip_origin_to_upper_leg_servo_origin_y" value="${-0.03175}" /> 		
		<xacro:property name="upper_leg_origin_offset_to_center_of_leg" value="${0.0075}" /> 
		
	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		
		<xacro:property name="upper_leg_length_between_joints" value="${0.100}" /> 

	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
		<xacro:property name="hip_upper_limit" value="${30 * pi/180}" /> 
		<xacro:property name="hip_lower_limit" value="${-30 * pi/180}" /> 
		<xacro:property name="upper_leg_upper_limit" value="${180 * pi/180}" /> 
		<xacro:property name="upper_leg_lower_limit" value="${-180 * pi/180}" /> 		
		<xacro:property name="lower_leg_upper_limit" value="${180 * pi/180}" /> 
		<xacro:property name="lower_leg_lower_limit" value="${-180 * pi/180}" />
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

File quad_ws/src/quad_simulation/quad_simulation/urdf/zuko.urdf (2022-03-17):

<?xml version="1.0" ?>
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
<robot name="zuko">
  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
  <link name="base_link">
    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
    <inertial>
      <mass value="0.6"/>
      <origin rpy="0 0 0" xyz="0 0 0"/>
      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
    </inertial>
  </link>
  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
  <link name="side_left_link">
    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
    <inertial>
      <mass value="0.6"/>
      <origin rpy="0 0 0" xyz="0 0 0"/>
      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
    </inertial>
  </link>
  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
  <link name="side_right_link">
    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
    <inertial>
      <mass value="0.6"/>
      <origin rpy="0 0 0" xyz="0 0 0"/>
      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
    </inertial>
  </link>
  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
  <link name="center_back_link">
    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
    <inertial>
      <mass value="0.6"/>
      <origin rpy="0 0 0" xyz="0 0 0"/>
      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
    </inertial>
  </link>
  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
  <link name="bridge_front_link">
    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
    <inertial>
      <mass value="0.6"/>
      <origin rpy="0 0 0" xyz="0 0 0"/>
      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
    </inertial>
  </link>
  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
  <link name="bridge_back_link">
    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
    <inertial>
      <mass value="0.6"/>
      <origin rpy="0 0 0" xyz="0 0 0"/>
      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
    </inertial>
  </link>
  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
  <link name="face_link">
    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
    <inertial>
      <mass value="0.6"/>
      <origin rpy="0 0 0" xyz="0 0 0"/>
      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
    </inertial>
  </link>
  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
  <link name="butt_link">
    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
    <inertial>
      <mass value="0.6"/>
      <origin rpy="0 0 0" xyz="0 0 0"/>
      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
    </inertial>
  </link>
  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
  <link name="electronics_cover_link">
    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
    <inertial>
      <mass value="0.6"/>
      <origin rpy="0 0 0" xyz="0 0 0"/>
      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
    </inertial>
  </link>
  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
  <link name="battery_cover_link">
    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
    <inertial>
      <mass value="0.6"/>
      <origin rpy="0 0 0" xyz="0 0 0"/>
      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
    </inertial>
  </link>
  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
  <link name="tail_link">
    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
    <inertial>
      <mass value="0.6"/>
      <origin rpy="0 0 0" xyz="0 0 0"/>
      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
    </inertial>
  </link>
  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
  <joint name="side_left_joint" type="fixed">
    <origin rpy="0 0 0" xyz="-0.16599999999999998 0.060 0.015"/>
    <parent link="base_link"/>
    <child link="side_left_link"/>
  </joint>
  <joint name="side_right_joint" type="fixed">
    <origin rpy="0 0 0" xyz="-0.018 -0.060 0.015"/>
    <parent link="base_link"/>
    <child link="side_right_link"/>
  </joint>
  <joint name="center_back_joint" type="fixed">
    <origin rpy="0 0 0" xyz="-0.18399999999999997 0 0"/>
    <parent link="base_link"/>
    <child link="center_back_link"/>
  </joint>
  <joint name="bridge_front_joint" type="fixed">
    <origin rpy="0 0 0" xyz="0.0535 0 -0.010"/>
    <parent link="base_link"/>
    <child link="bridge_front_link"/>
  </joint>
  <joint name="bridge_back_joint" type="fixed">
    <origin rpy="0 0 0" xyz="0 0 -0.010"/>
    <parent link="center_back_link"/>
    <child link="bridge_back_link"/>
  </joint>
  <joint name="face_joint" type="fixed">
    <origin rpy="0 0 0" xyz="0 0 0"/>
    <parent link="bridge_front_link"/>
    <child link="face_link"/>
  </joint>
  <joint name="butt_joint" type="fixed">
    <origin rpy="0 0 0" xyz="-0.0535 0 0"/>
    <parent link="bridge_back_link"/>
    <child link="butt_link"/>
  </joint>
  <joint name="electronics_cover_joint" type="fixed">
    <origin rpy="0 0 3.141592653589793" xyz="-0.092 0 0.019"/>
    <parent link="base_link"/>
    <child link="electronics_cover_link"/>
  </joint>
  <joint name="battery_cover_joint" type="fixed">
    <origin rpy="3.141592653589793 0 3.141592653589793" xyz="-0.09375 0 -0.039"/>
    <parent link="base_link"/>
    <child link="battery_cover_link"/>
  </joint>
  <joint name="tail_joint" type="fixed">
    <origin rpy="0 0 0 " xyz="-0.012419 0 0.025687"/>
    <parent link="butt_link"/>
    <child link="tail_link"/>
  </joint>
  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
  <link name="front_left_hip_link">
    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
    <inertial>
      <mass value="0.6"/>
      <origin rpy="0 0 0" xyz="0 0 0"/>
      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
    </inertial>
  </link>
  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
  <joint name="front_left_hip_rev_joint" type="revolute">
    <axis xyz="-1 0 0"/>
    <origin rpy="0 0 3.141592653589793" xyz="0.002 0.0455 0"/>
    <parent link="base_link"/>
    <child link="front_left_hip_link"/>
    <limit effort="4.0" lower="-0.5235987755982988" upper="0.5235987755982988" velocity="4.0"/>
    <joint_properties damping="0.0" friction="0.0"/>
  </joint>
  <link name="front_left_upper_leg_link">
    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
    <inertial>
      <mass value="0.6"/>
      <origin rpy="0 0 0" xyz="0 0 0"/>
      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
    </inertial>
  </link>
  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
  <joint name="front_left_upper_leg_rev_joint" type="revolute">
    <axis xyz="0 1 0"/>
    <origin rpy="0 0 3.141592653589793" xyz="-0.0145 -0.03175 0"/>
    <parent link="front_left_hip_link"/>
    <child link="front_left_upper_leg_link"/>
    <limit effort="4.0" lower="-3.141592653589793" upper="3.141592653589793" velocity="4.0"/>
    <joint_properties damping="0.0" friction="0.0"/>
  </joint>
  <link name="front_left_lower_leg_link">
    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
    <inertial>
      <mass value="0.6"/>
      <origin rpy="0 0 0" xyz="0 0 0"/>
      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
    </inertial>
  </link>
  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

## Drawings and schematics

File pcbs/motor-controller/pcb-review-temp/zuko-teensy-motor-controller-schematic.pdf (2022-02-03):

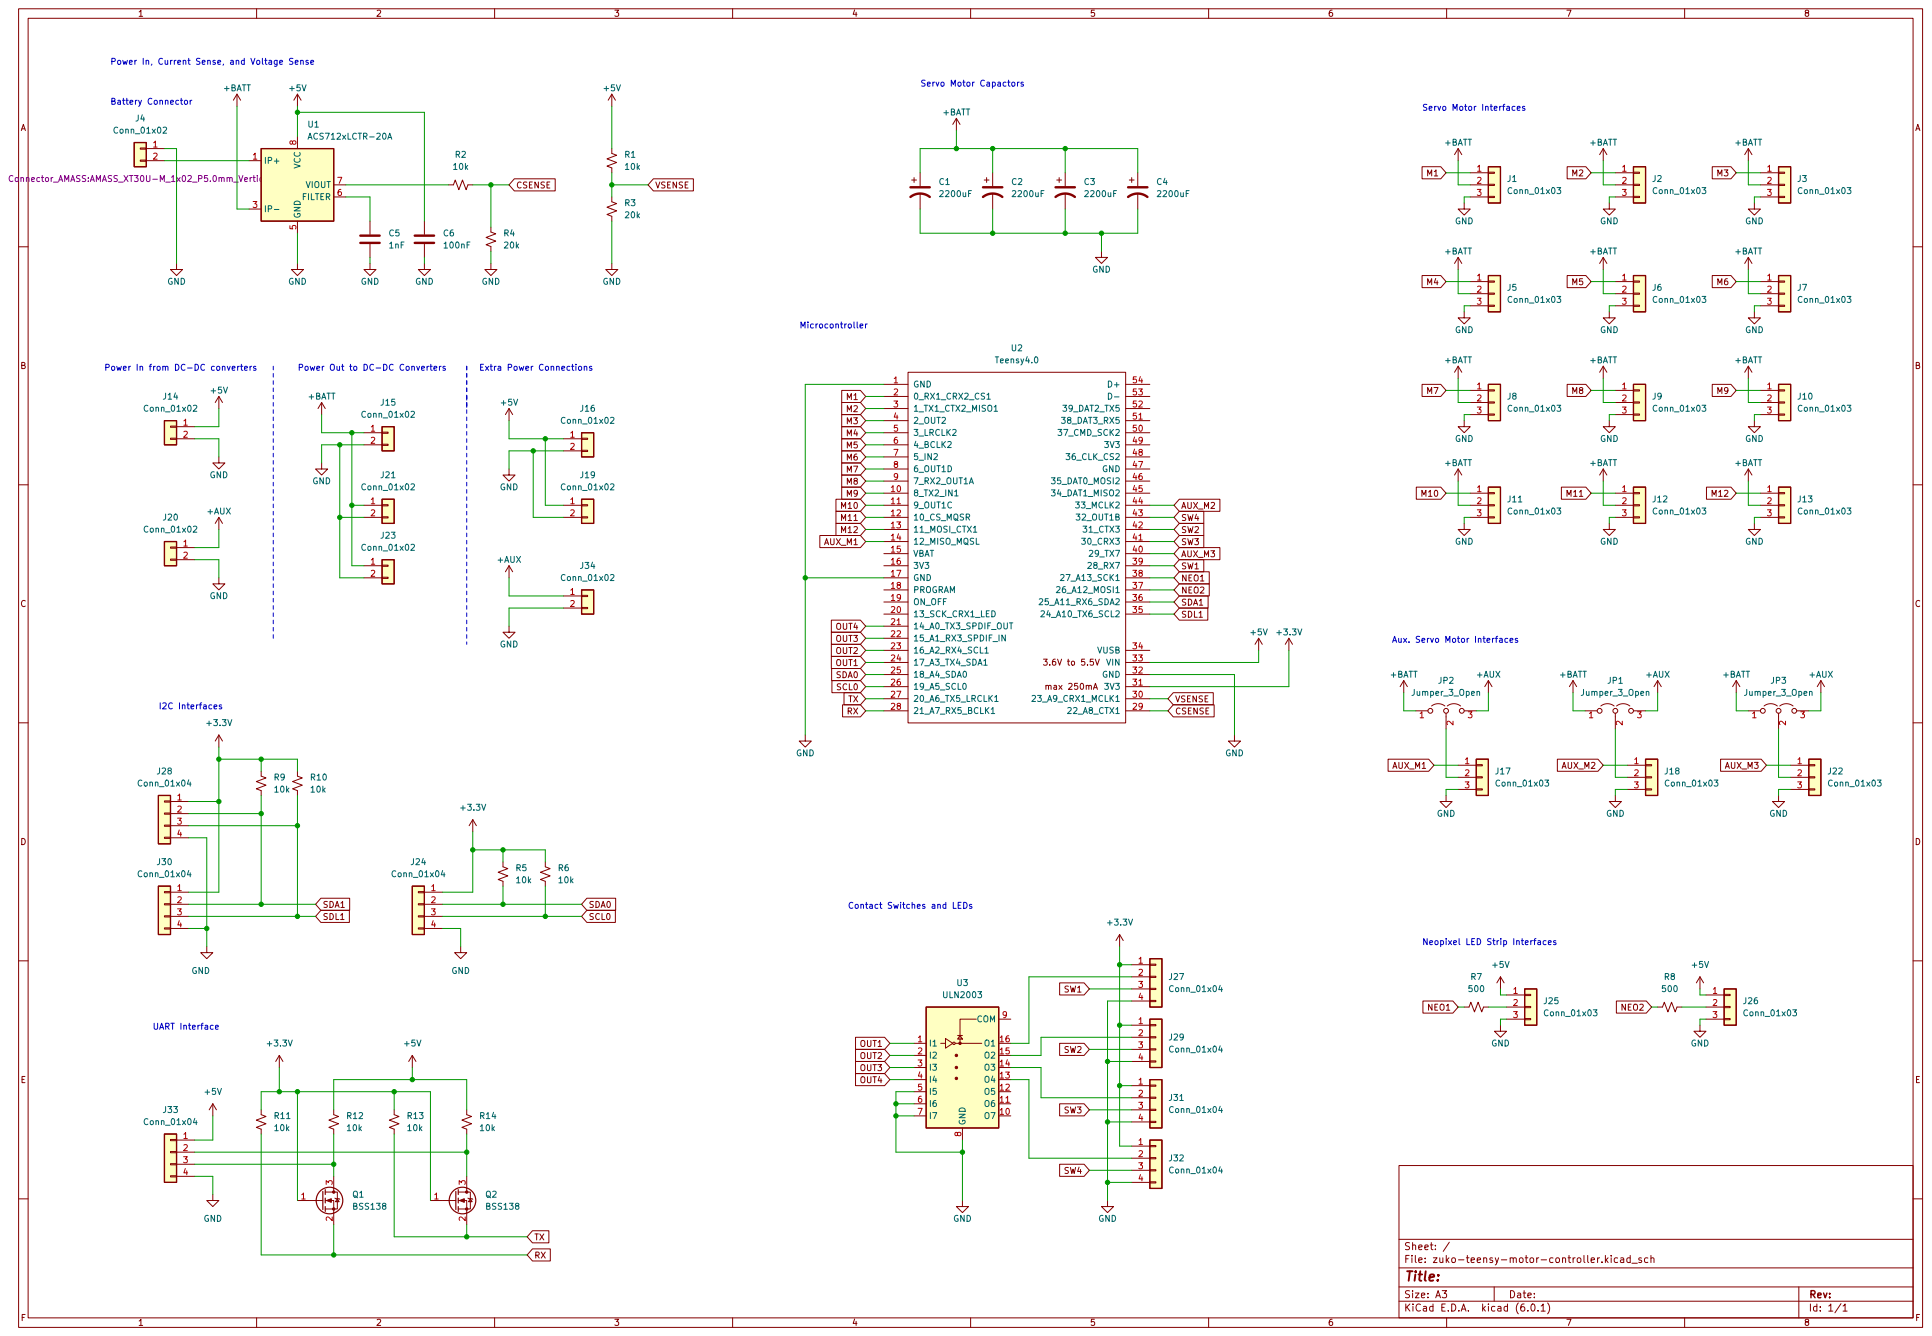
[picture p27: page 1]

Power In from DC-DC converters Power In, Current Sense, and Voltage Sense

SW1 Contact Switches and LEDs

File: zuko-teensy-motor-controller.kicad_sch Sheet: /

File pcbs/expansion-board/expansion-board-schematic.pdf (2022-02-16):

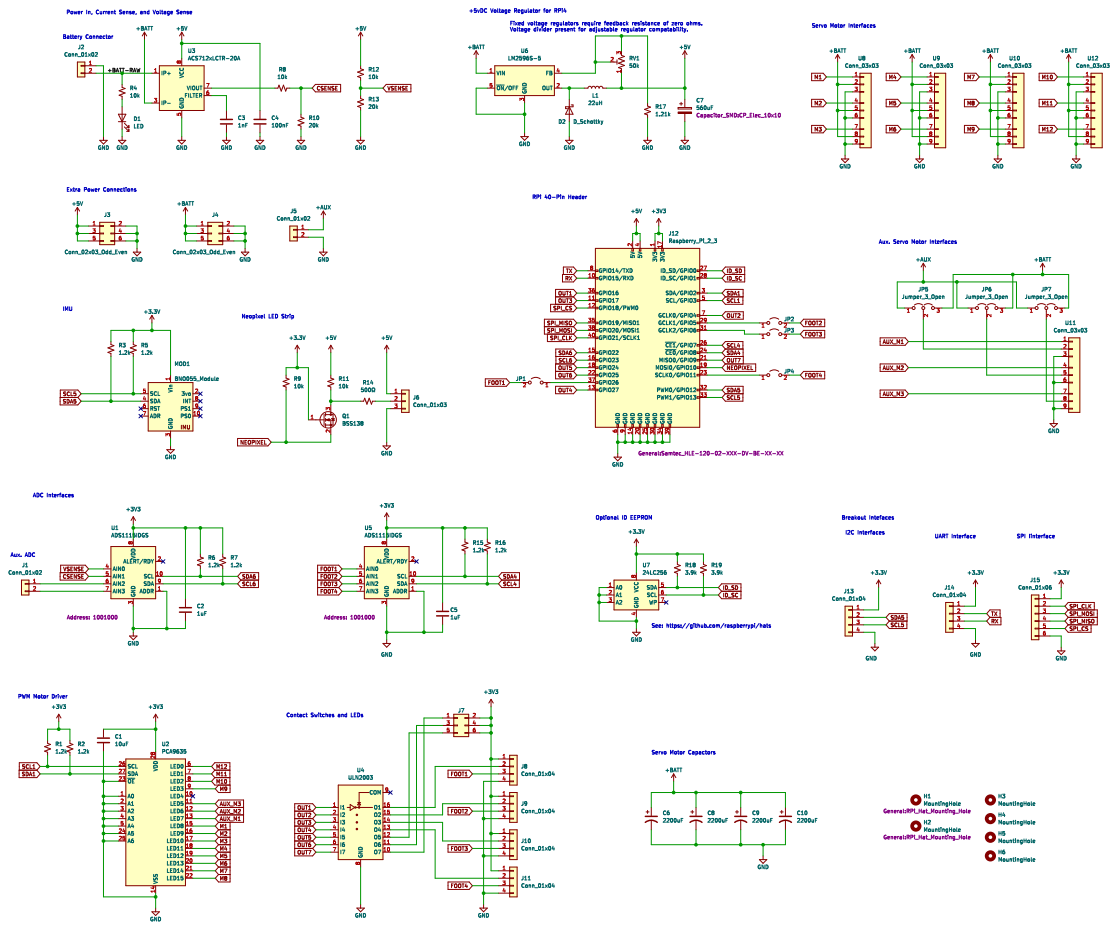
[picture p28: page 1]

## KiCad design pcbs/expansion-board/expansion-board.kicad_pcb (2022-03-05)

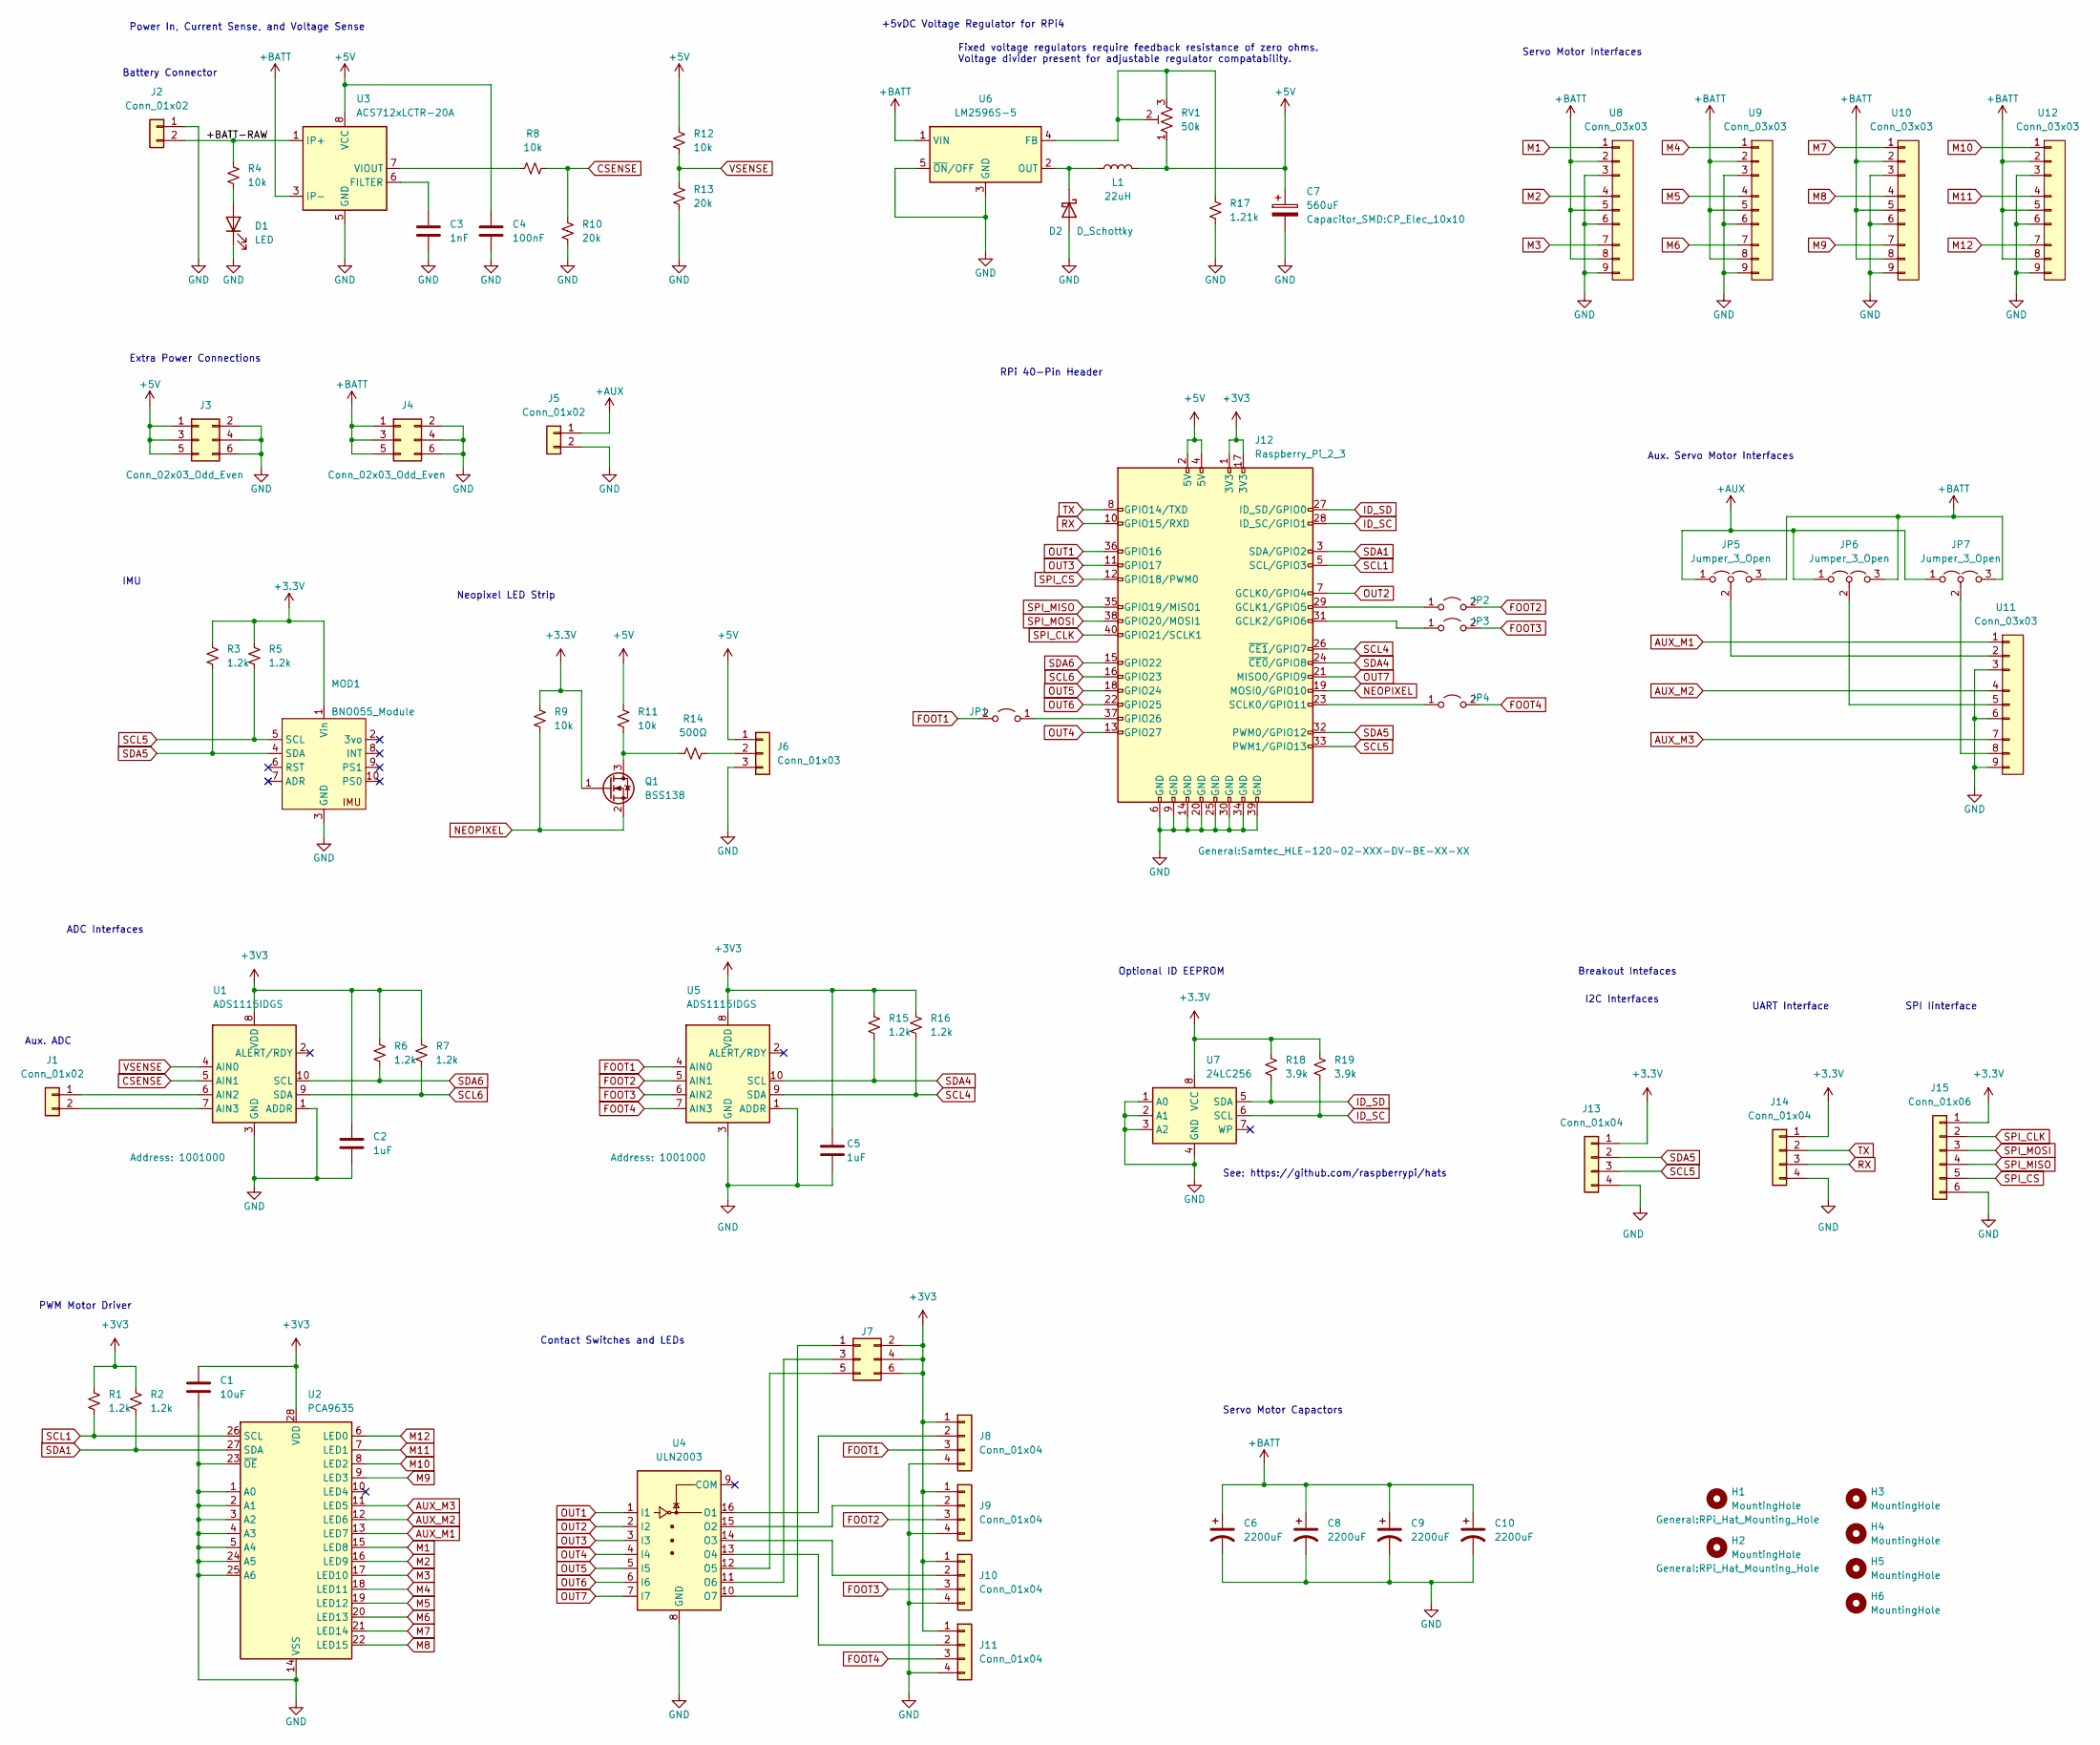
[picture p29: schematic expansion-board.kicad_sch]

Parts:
C1: 10uF; C_0805_2012Metric
C2, C5: 1uF; C_0805_2012Metric
C3: 1nF; C_0805_2012Metric
C4: 100nF; C_0805_2012Metric
C6, C8, C9, C10: 2200uF; CP_Radial_D10.0mm_P5.00mm
C7: 560uF; CP_Elec_10x10
D1: LED; LED_0805_2012Metric
D2: D_Schottky; D_SMC
H1, H2, H3, H4, H5, H6: MountingHole; RPi_Hat_Mounting_Hole
J1, J5: Conn_01x02; PinHeader_1x02_P2.54mm_Vertical
J2: Conn_01x02; AMASS_XT30U-M_1x02_P5.0mm_Vertical
J3, J4: Conn_02x03_Odd_Even; PinHeader_2x03_P2.54mm_Vertical
J6: Conn_01x03; PinHeader_1x03_P2.54mm_Vertical
J7: Conn_02x03_Counter_Clockwise; PinHeader_2x03_P2.54mm_Vertical
J8, J9, J10, J11, J13, J14: Conn_01x04; PinHeader_1x04_P2.54mm_Vertical
J12: Raspberry_Pi_2_3; Samtec_HLE-120-02-XXX-DV-BE-XX-XX
J15: Conn_01x06; PinHeader_1x06_P2.54mm_Vertical
JP1, JP2, JP3, JP4: Jumper_2_Open; SolderJumper-2_P1.3mm_Open_Pad1.0x1.5mm
JP5, JP6, JP7: Jumper_3_Open; SolderJumper-3_P1.3mm_Open_RoundedPad1.0x1.5mm
L1: 22uH; L_12x12mm_H6mm
MOD1: BNO055_Module; BNO055 Module
Q1: BSS138; SOT-23
R1, R2, R3, R5, R6, R7, R15, R16: 1.2k; R_0805_2012Metric
R4, R8, R9, R11, R12: 10k; R_0805_2012Metric
R10, R13: 20k; R_0805_2012Metric
R14: 500Ω; R_0805_2012Metric
R17: 1.21k; R_0805_2012Metric
R18, R19: 3.9k; R_0805_2012Metric
RV1: 50k; Precision_pot
U1, U5: ADS1115IDGS; TSSOP-10_3x3mm_P0.5mm
U2: PCA9635; TSSOP-28_4.4x9.7mm_P0.65mm
U3: ACS712xLCTR-20A; SOIC-8_3.9x4.9mm_P1.27mm
U4: ULN2003; SOIC-16_3.9x9.9mm_P1.27mm
U6: LM2596S-5; TO-263-5_TabPin3
U7: 24LC256; SOIC-8_3.9x4.9mm_P1.27mm
U8, U9, U10, U11, U12: Conn_03x03

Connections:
+5V: C4.1, C7.1, J3.1, J3.3, J3.5, J6.1, J12.2 (5V), J12.4 (5V), L1.1, R11.1, R12.1, RV1.1, U3.8 (VCC)
+AUX: J5.1, JP5.1 (A), JP6.1 (A), JP7.1 (A)
+BATT: C6.1, C8.1, C9.1, C10.1, J4.1, J4.3, J4.5, JP5.3 (B), JP6.3 (B), JP7.3 (B), U3.3 (IP-), U3.4 (IP-), U6.1 (VIN), U8.2, U8.5, U8.8, U9.2, U9.5, U9.8, U10.2, U10.5, U10.8, U12.2, U12.5, U12.8
/+BATT-RAW: J2.2, R4.2, U3.1 (IP+), U3.2 (IP+)
AUX_M1: U2.13 (LED7), U11.1
AUX_M2: U2.12 (LED6), U11.4
AUX_M3: U2.11 (LED5), U11.7
CSENSE: R8.2, R10.1, U1.5 (AIN1)
FOOT1: J8.3, JP1.2 (B), U5.4 (AIN0)
FOOT2: J9.3, JP2.2 (B), U5.5 (AIN1)
FOOT3: J10.3, JP3.2 (B), U5.6 (AIN2)
FOOT4: J11.3, JP4.2 (B), U5.7 (AIN3)
GND: C1.2, C2.2, C3.2, C4.2, C5.2, C6.2, C7.2, C8.2, C9.2, C10.2, D1.1 (K), D2.2 (A), J2.1, J3.2, J3.4, J3.6, J4.2, J4.4, J4.6, J5.2, J6.3, J8.4, J9.4, J10.4, J11.4, J12.6 (GND), J12.9 (GND), J12.14 (GND), J12.20 (GND), J12.25 (GND), J12.30 (GND), J12.34 (GND), J12.39 (GND), J13.4, J14.4, J15.6, MOD1.3 (GND), R10.2, R13.2, R17.1, U1.1 (ADDR), U1.3 (GND), U2.1 (A0), U2.2 (A1), U2.3 (A2), U2.4 (A3), U2.5 (A4), U2.14 (VSS), U2.23 (~OE), U2.24 (A5), U2.25 (A6), U3.5 (GND), U4.8 (GND), U5.1 (ADDR), U5.3 (GND), U6.3 (GND), U6.5 (~ON/OFF), U7.1 (A0), U7.2 (A1), U7.3 (A2), U7.4 (GND), U8.3, U8.6, U8.9, U9.3, U9.6, U9.9, U10.3, U10.6, U10.9, U11.3, U11.6, U11.9, U12.3, U12.6, U12.9
ID_SC: J12.28 (ID_SC/GPIO1), R19.2, U7.6 (SCL)
ID_SD: J12.27 (ID_SD/GPIO0), R18.2, U7.5 (SDA)
M1: U2.15 (LED8), U8.1
M2: U2.16 (LED9), U8.4
M3: U2.17 (LED10), U8.7
M4: U2.18 (LED11), U9.1
M5: U2.19 (LED12), U9.4
M6: U2.20 (LED13), U9.7
M7: U2.21 (LED14), U10.1
M8: U2.22 (LED15), U10.4
M9: U2.9 (LED3), U10.7
M10: U2.8 (LED2), U12.1
M11: U2.7 (LED1), U12.4
M12: U2.6 (LED0), U12.7
NEOPIXEL: J12.19 (MOSI0/GPIO10), Q1.2 (S), R9.2
unnamed: C3.1, U3.6 (FILTER)
unnamed: D1.2 (A), R4.1
unnamed: D2.1 (K), L1.2, U6.2 (OUT)
unnamed: J1.1, U1.6 (AIN2)
unnamed: J1.2, U1.7 (AIN3)
unnamed: J6.2, R14.1
unnamed: J7.1, U4.10 (O7)
unnamed: J7.3, U4.11 (O6)
unnamed: J7.5, U4.12 (O5)
unnamed: J8.2, U4.16 (O1)
unnamed: J9.2, U4.15 (O2)
unnamed: J10.2, U4.14 (O3)
unnamed: J11.2, U4.13 (O4)
unnamed: J12.23 (SCLK0/GPIO11), JP4.1 (A)
unnamed: J12.29 (GCLK1/GPIO5), JP2.1 (A)
unnamed: J12.31 (GCLK2/GPIO6), JP3.1 (A)
unnamed: J12.37 (GPIO26), JP1.1 (A)
unnamed: JP5.2 (C), U11.2
unnamed: JP6.2 (C), U11.5
unnamed: JP7.2 (C), U11.8
unnamed: Q1.3 (D), R11.2, R14.2
unnamed: R8.1, U3.7 (VIOUT)
unnamed: R17.2, RV1.2, RV1.3, U6.4 (FB)
OUT1: J12.36 (GPIO16), U4.1 (I1)
OUT2: J12.7 (GCLK0/GPIO4), U4.2 (I2)
OUT3: J12.11 (GPIO17), U4.3 (I3)
OUT4: J12.13 (GPIO27), U4.4 (I4)
OUT5: J12.18 (GPIO24), U4.5 (I5)
OUT6: J12.22 (GPIO25), U4.6 (I6)
OUT7: J12.21 (MISO0/GPIO9), U4.7 (I7)
RX: J12.10 (GPIO15/RXD), J14.3
SCL1: J12.5 (SCL/GPIO3), R1.2, U2.26 (SCL)
SCL4: J12.26 (~CE1/GPIO7), R16.2, U5.9 (SDA)
SCL5: J12.33 (PWM1/GPIO13), J13.3, MOD1.5 (SCL), R5.2
SCL6: J12.16 (GPIO23), R7.2, U1.9 (SDA)
SDA1: J12.3 (SDA/GPIO2), R2.2, U2.27 (SDA)
SDA4: J12.24 (~CE0/GPIO8), R15.2, U5.10 (SCL)
SDA5: J12.32 (PWM0/GPIO12), J13.2, MOD1.4 (SDA), R3.2
SDA6: J12.15 (GPIO22), R6.2, U1.10 (SCL)
SPI_CLK: J12.40 (GPIO21/SCLK1), J15.2
SPI_CS: J12.12 (GPIO18/PWM0), J15.5
SPI_MISO: J12.35 (GPIO19/MISO1), J15.4
SPI_MOSI: J12.38 (GPIO20/MOSI1), J15.3
TX: J12.8 (GPIO14/TXD), J14.2
VSENSE: R12.2, R13.1, U1.4 (AIN0)

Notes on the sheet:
Breakout Intefaces
SPI Iinterface
ADC Interfaces
Extra Power Connections
PWM Motor Driver
Aux. ADC
+5vDC Voltage Regulator for RPi4
See: https://github.com/raspberrypi/hats
Power In, Current Sense, and Voltage Sense
Fixed voltage regulators require feedback resistance of zero ohms. Voltage divider present for adjustable regulator compatability.
Servo Motor Capactors
UART Interface
Optional ID EEPROM
Servo Motor Interfaces
Neopixel LED Strip
Battery Connector
Aux. Servo Motor Interfaces
Contact Switches and LEDs
I2C Interfaces
IMU
RPi 40-Pin Header

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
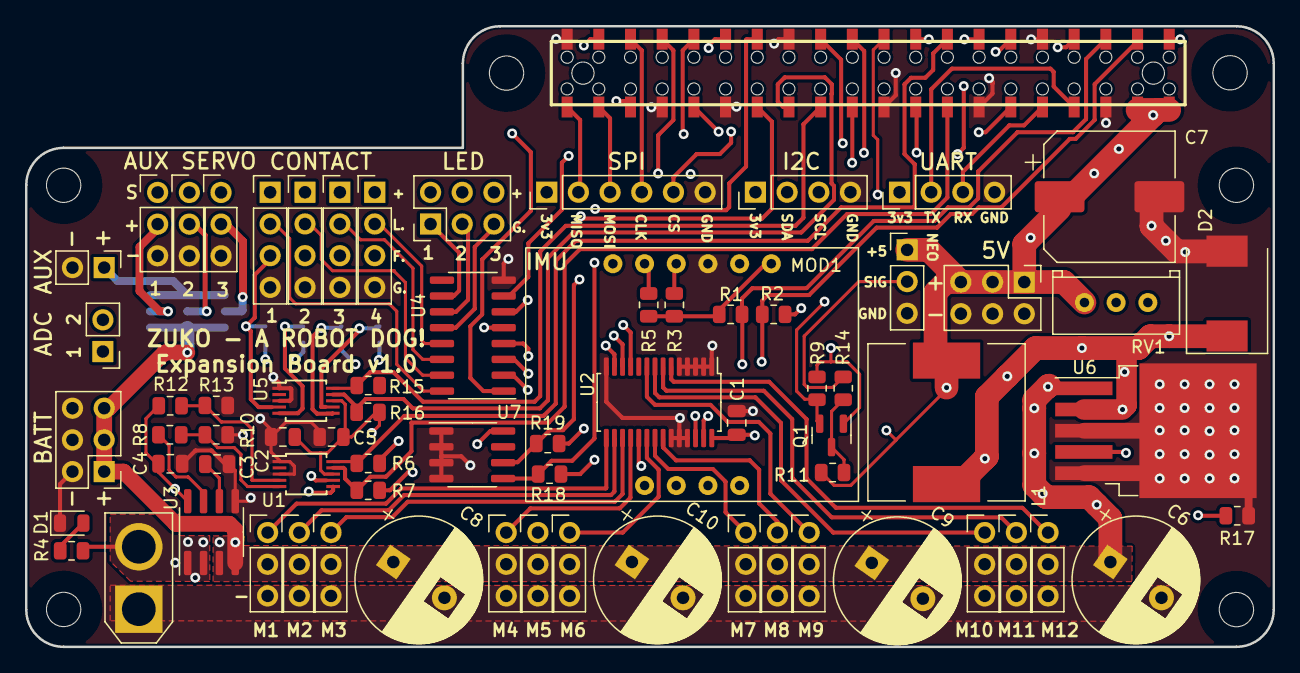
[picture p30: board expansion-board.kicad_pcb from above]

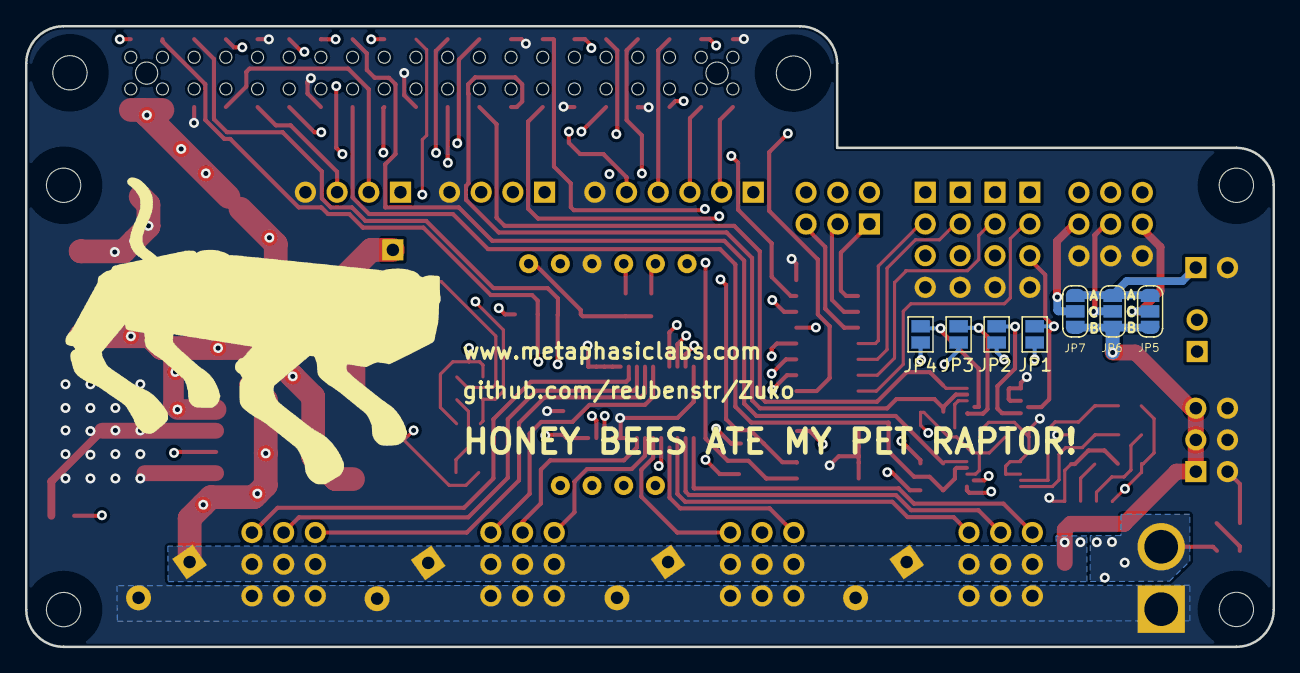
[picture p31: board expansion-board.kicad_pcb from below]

Board: 4 copper layers, 100.0 x 49.8 mm, 75 parts (7 on the bottom side), 74 nets.

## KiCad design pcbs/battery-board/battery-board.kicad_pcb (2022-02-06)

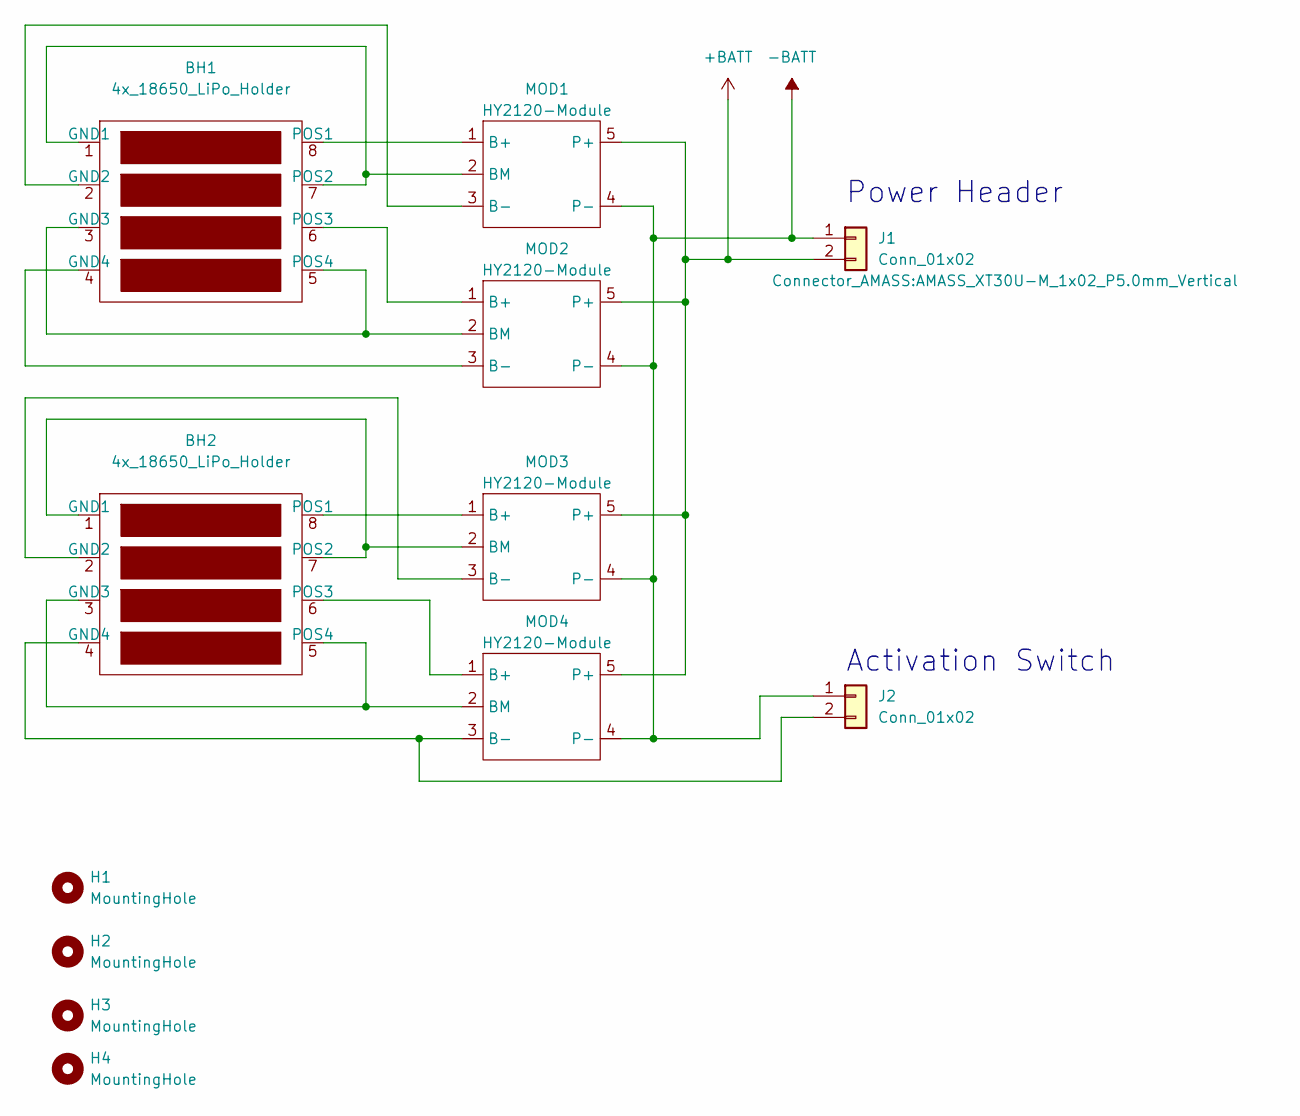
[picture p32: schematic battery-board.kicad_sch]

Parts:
BH1, BH2: 4x_18650_LiPo_Holder; 4x_18650_LiPo_Module
H1, H2, H3, H4: MountingHole; MountingHole_3.2mm_M3
J1: Conn_01x02; AMASS_XT30U-M_1x02_P5.0mm_Vertical
J2: Conn_01x02; PinHeader_1x02_P2.54mm_Vertical
MOD1, MOD2, MOD3, MOD4: HY2120-Module; HY2120

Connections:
+BATT: J1.2, MOD1.5 (P+), MOD2.5 (P+), MOD3.5 (P+), MOD4.5 (P+)
-BATT: J1.1, J2.1, MOD1.4 (P-), MOD2.4 (P-), MOD3.4 (P-), MOD4.4 (P-)
unnamed: BH1.1 (GND1), BH1.7 (POS2), MOD1.2 (BM)
unnamed: BH1.2 (GND2), MOD1.3 (B-)
unnamed: BH1.3 (GND3), BH1.5 (POS4), MOD2.2 (BM)
unnamed: BH1.4 (GND4), MOD2.3 (B-)
unnamed: BH1.6 (POS3), MOD2.1 (B+)
unnamed: BH1.8 (POS1), MOD1.1 (B+)
unnamed: BH2.1 (GND1), BH2.7 (POS2), MOD3.2 (BM)
unnamed: BH2.2 (GND2), MOD3.3 (B-)
unnamed: BH2.3 (GND3), BH2.5 (POS4), MOD4.2 (BM)
unnamed: BH2.4 (GND4), J2.2, MOD4.3 (B-)
unnamed: BH2.6 (POS3), MOD4.1 (B+)
unnamed: BH2.8 (POS1), MOD3.1 (B+)

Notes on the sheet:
Power Header
Activation Switch

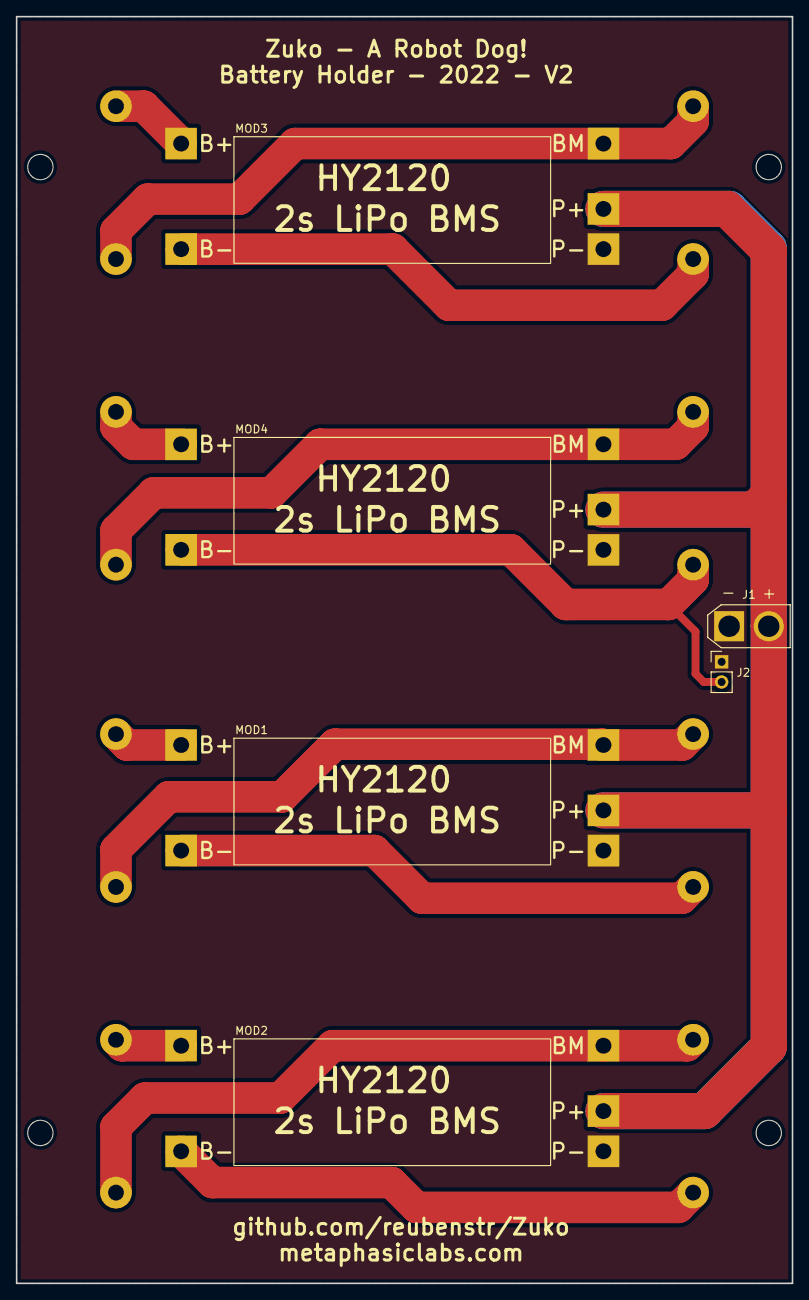
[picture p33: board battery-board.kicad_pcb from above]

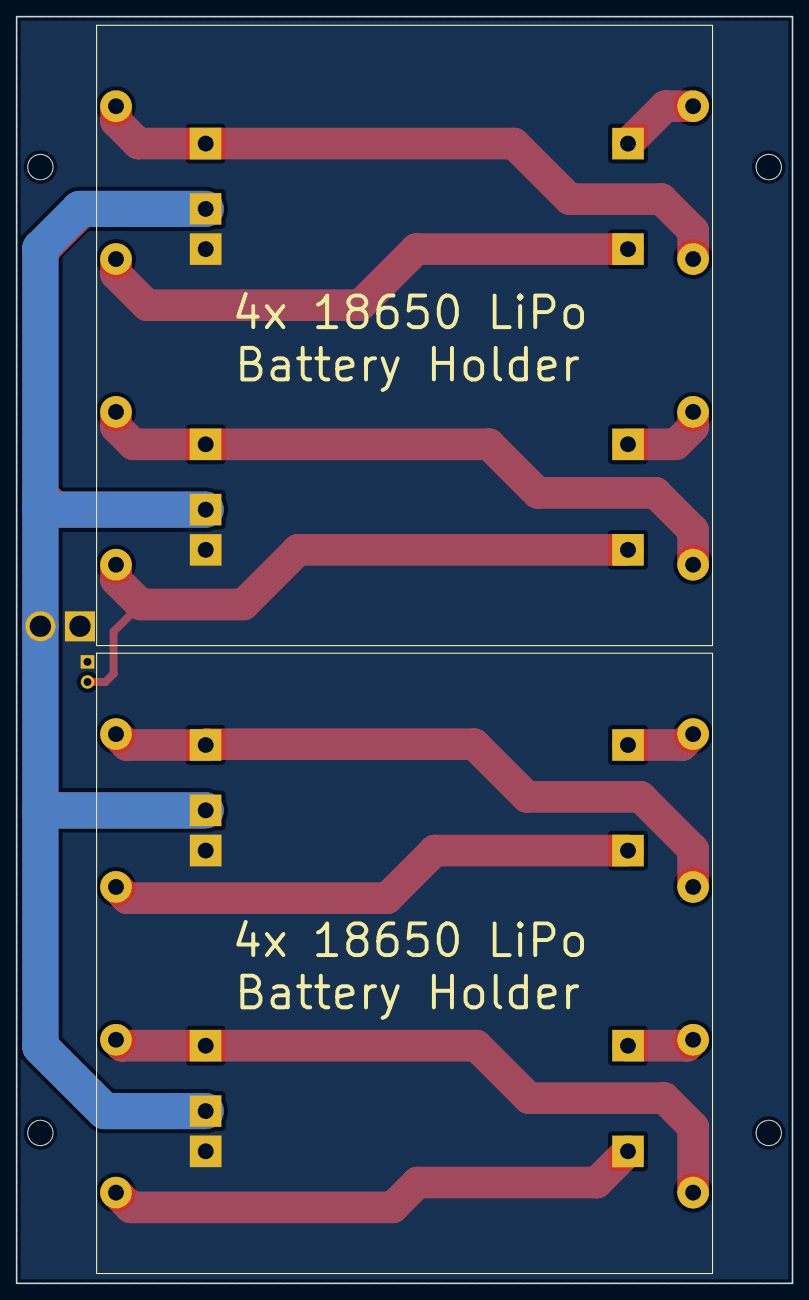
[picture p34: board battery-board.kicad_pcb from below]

Board: 2 copper layers, 98.0 x 160.0 mm, 12 parts (2 on the bottom side), 14 nets.

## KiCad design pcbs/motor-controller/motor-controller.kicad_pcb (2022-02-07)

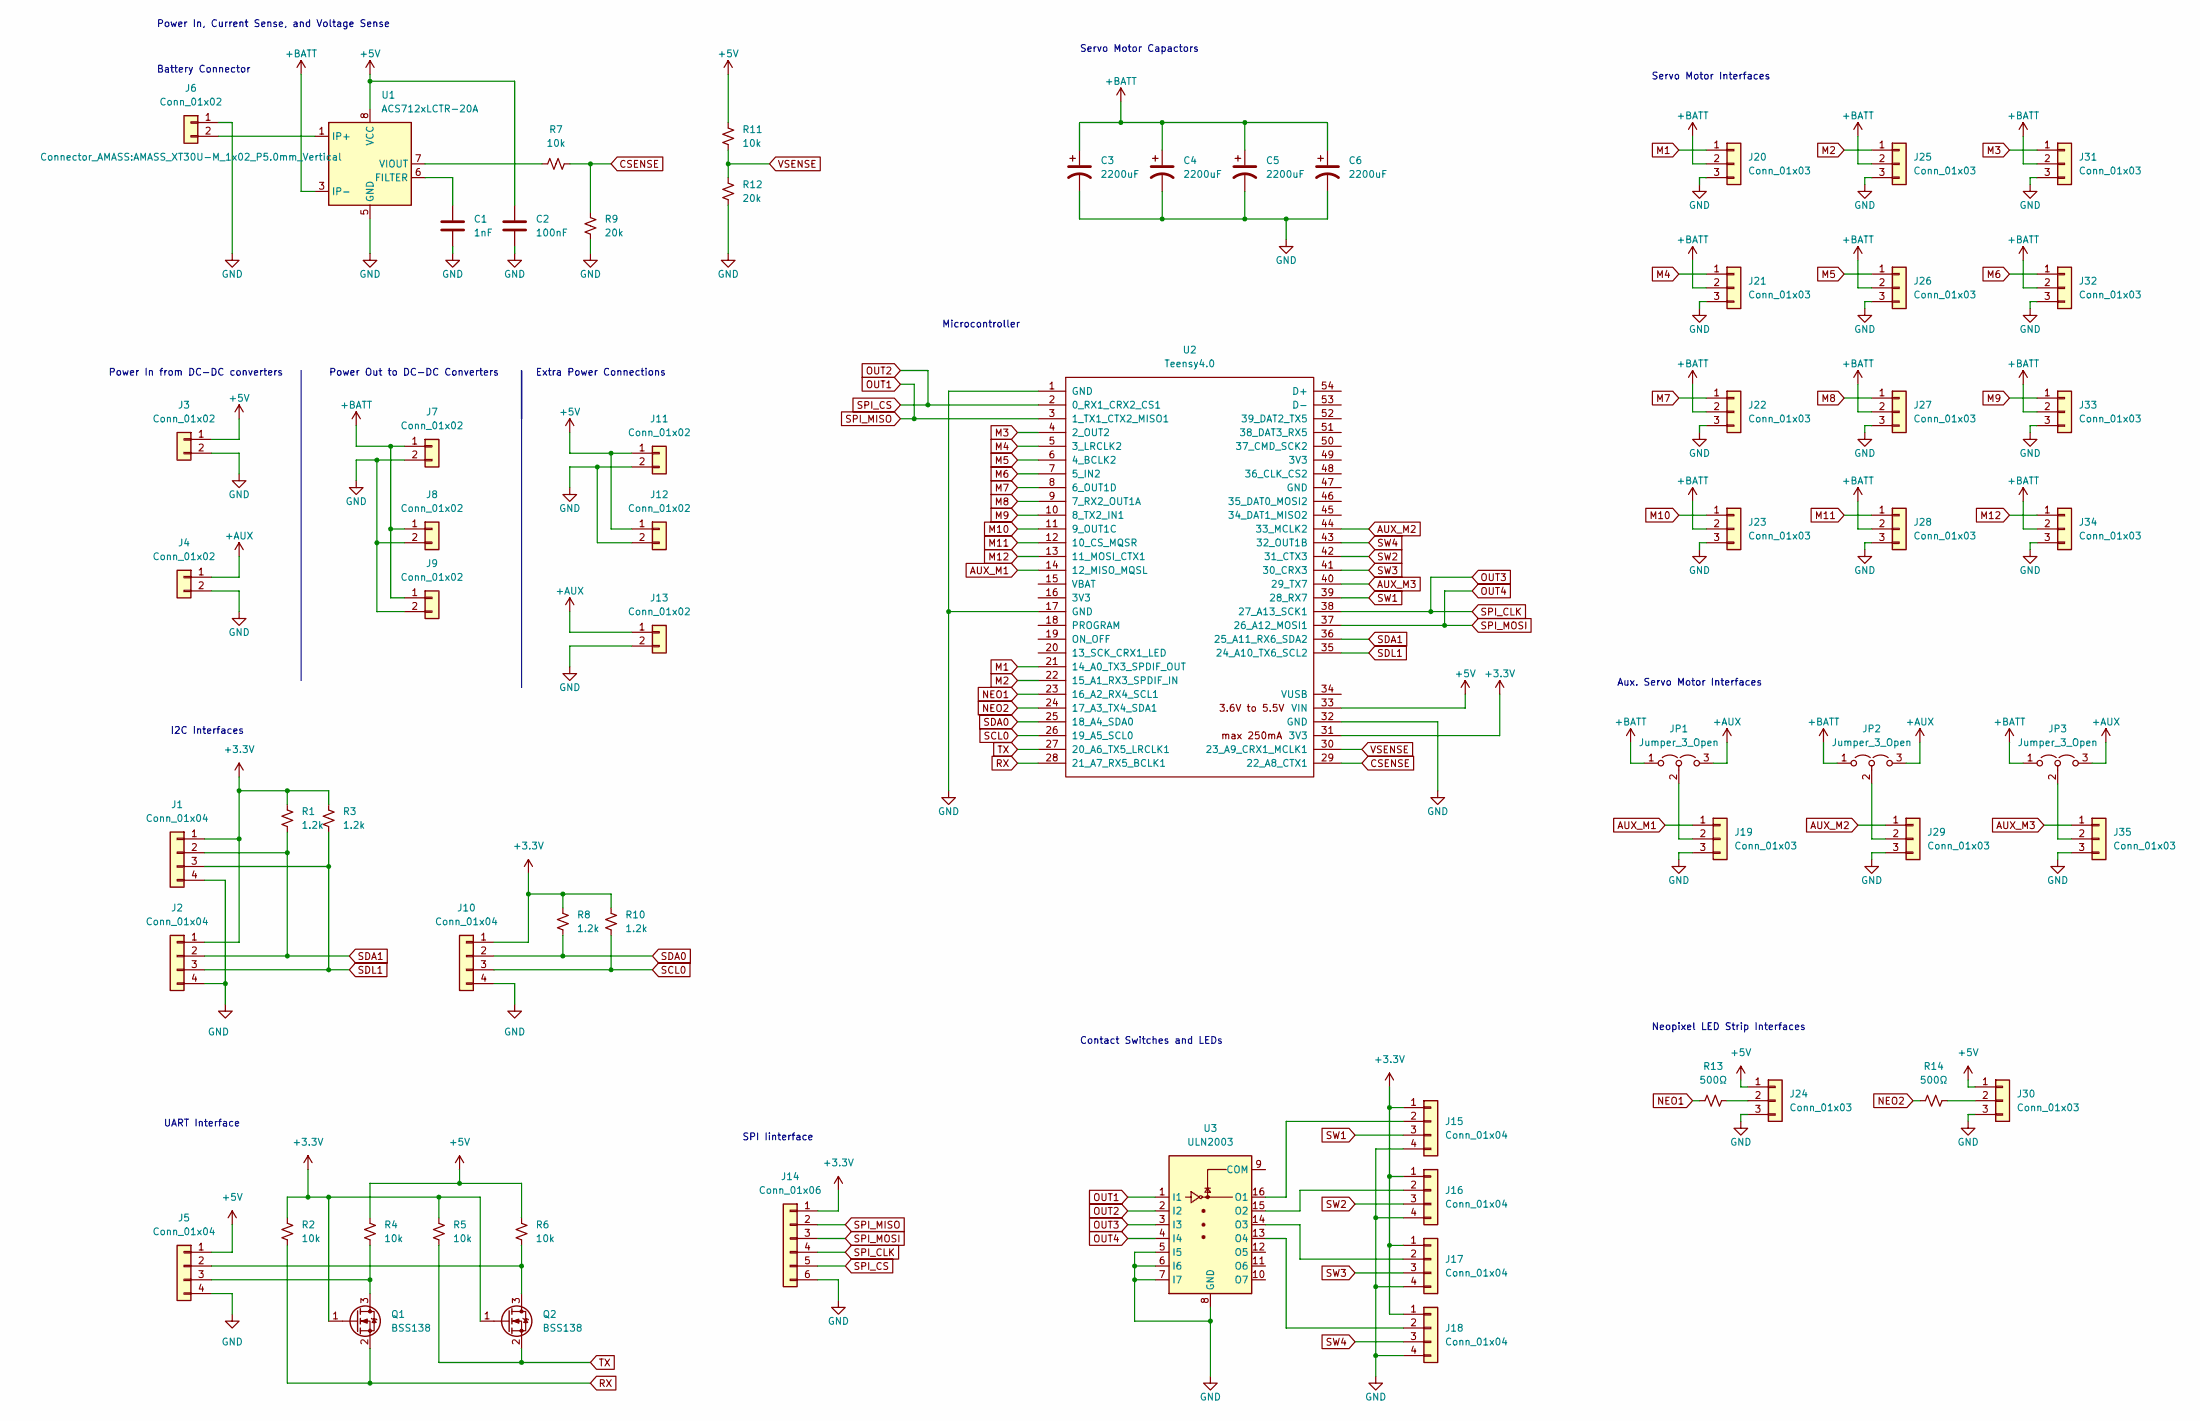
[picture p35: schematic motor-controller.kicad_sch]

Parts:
C1: 1nF; C_1206_3216Metric_Pad1.33x1.80mm_HandSolder
C2: 100nF; C_1206_3216Metric_Pad1.33x1.80mm_HandSolder
C3, C4, C5, C6: 2200uF; CP_Radial_D10.0mm_P5.00mm
J1, J2, J5, J10, J15, J16, J17, J18: Conn_01x04; PinHeader_1x04_P2.54mm_Vertical
J3, J4, J7, J8, J9, J11, J12, J13: Conn_01x02; PinHeader_1x02_P2.54mm_Vertical
J6: Conn_01x02; AMASS_XT30U-M_1x02_P5.0mm_Vertical
J14: Conn_01x06; PinHeader_1x06_P2.54mm_Vertical
J19, J20, J21, J22, J23, J24, J25, J26, J27, J28, J29, J30, J31, J32, J33, J34, J35: Conn_01x03; PinHeader_1x03_P2.54mm_Vertical
JP1, JP2, JP3: Jumper_3_Open; PinHeader_1x03_P2.54mm_Vertical
Q1, Q2: BSS138; SOT-23
R1, R3, R8, R10: 1.2k; R_1206_3216Metric_Pad1.30x1.75mm_HandSolder
R2, R4, R5, R6, R7, R11: 10k; R_1206_3216Metric_Pad1.30x1.75mm_HandSolder
R9, R12: 20k; R_1206_3216Metric_Pad1.30x1.75mm_HandSolder
R13, R14: 500Ω; R_1206_3216Metric_Pad1.30x1.75mm_HandSolder
U1: ACS712xLCTR-20A; SOIC-8_3.9x4.9mm_P1.27mm
U2: Teensy4.0; Teensy40
U3: ULN2003; SOIC-16_3.9x9.9mm_P1.27mm

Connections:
+3V3: J1.1, J2.1, J10.1, J14.1, J15.1, J16.1, J17.1, J18.1, Q1.1 (G), Q2.1 (G), R1.1, R2.1, R3.1, R5.1, R8.1, R10.1, U2.31 (3V3)
+5V: C2.1, J3.1, J5.1, J11.1, J12.1, J24.1, J30.1, R4.1, R6.1, R11.1, U1.8 (VCC), U2.33 (VIN)
+AUX: J4.1, J13.1, JP1.3 (B), JP2.3 (B), JP3.3 (B)
+BATT: C3.1, C4.1, C5.1, C6.1, J7.1, J8.1, J9.1, J20.2, J21.2, J22.2, J23.2, J25.2, J26.2, J27.2, J28.2, J31.2, J32.2, J33.2, J34.2, JP1.1 (A), JP2.1 (A), JP3.1 (A), U1.3 (IP-), U1.4 (IP-)
AUX_M1: J19.1, U2.14 (12_MISO_MQSL)
AUX_M2: J29.1, U2.44 (33_MCLK2)
AUX_M3: J35.1, U2.40 (29_TX7)
CSENSE: R7.2, R9.1, U2.29 (22_A8_CTX1)
GND: C1.2, C2.2, C3.2, C4.2, C5.2, C6.2, J1.4, J2.4, J3.2, J4.2, J5.4, J6.1, J7.2, J8.2, J9.2, J10.4, J11.2, J12.2, J13.2, J14.6, J15.4, J16.4, J17.4, J18.4, J19.3, J20.3, J21.3, J22.3, J23.3, J24.3, J25.3, J26.3, J27.3, J28.3, J29.3, J30.3, J31.3, J32.3, J33.3, J34.3, J35.3, R9.2, R12.2, U1.5 (GND), U2.1 (GND), U2.17 (GND), U2.32 (GND), U3.5 (I5), U3.6 (I6), U3.7 (I7), U3.8 (GND)
M1: J20.1, U2.21 (14_A0_TX3_SPDIF_OUT)
M2: J25.1, U2.22 (15_A1_RX3_SPDIF_IN)
M3: J31.1, U2.4 (2_OUT2)
M4: J21.1, U2.5 (3_LRCLK2)
M5: J26.1, U2.6 (4_BCLK2)
M6: J32.1, U2.7 (5_IN2)
M7: J22.1, U2.8 (6_OUT1D)
M8: J27.1, U2.9 (7_RX2_OUT1A)
M9: J33.1, U2.10 (8_TX2_IN1)
M10: J23.1, U2.11 (9_OUT1C)
M11: J28.1, U2.12 (10_CS_MQSR)
M12: J34.1, U2.13 (11_MOSI_CTX1)
NEO1: R13.2, U2.23 (16_A2_RX4_SCL1)
NEO2: R14.2, U2.24 (17_A3_TX4_SDA1)
unnamed: C1.1, U1.6 (FILTER)
unnamed: J5.2, Q2.3 (D), R6.2
unnamed: J5.3, Q1.3 (D), R4.2
unnamed: J6.2, U1.1 (IP+), U1.2 (IP+)
unnamed: J15.2, U3.16 (O1)
unnamed: J16.2, U3.15 (O2)
unnamed: J17.2, U3.14 (O3)
unnamed: J18.2, U3.13 (O4)
unnamed: J19.2, JP1.2 (C)
unnamed: J24.2, R13.1
unnamed: J29.2, JP2.2 (C)
unnamed: J30.2, R14.1
unnamed: J35.2, JP3.2 (C)
unnamed: R7.1, U1.7 (VIOUT)
RX: Q1.2 (S), R2.2, U2.28 (21_A7_RX5_BCLK1)
SCL0: J10.3, R10.2, U2.26 (19_A5_SCL0)
SDA0: J10.2, R8.2, U2.25 (18_A4_SDA0)
SDA1: J1.2, J2.2, R1.2, U2.36 (25_A11_RX6_SDA2)
SDL1: J1.3, J2.3, R3.2, U2.35 (24_A10_TX6_SCL2)
SPI_CLK: J14.4, U2.38 (27_A13_SCK1), U3.3 (I3)
SPI_CS: J14.5, U2.2 (0_RX1_CRX2_CS1), U3.2 (I2)
SPI_MISO: J14.2, U2.3 (1_TX1_CTX2_MISO1), U3.1 (I1)
SPI_MOSI: J14.3, U2.37 (26_A12_MOSI1), U3.4 (I4)
SW1: J15.3, U2.39 (28_RX7)
SW2: J16.3, U2.42 (31_CTX3)
SW3: J17.3, U2.41 (30_CRX3)
SW4: J18.3, U2.43 (32_OUT1B)
TX: Q2.2 (S), R5.2, U2.27 (20_A6_TX5_LRCLK1)
VSENSE: R11.2, R12.1, U2.30 (23_A9_CRX1_MCLK1)

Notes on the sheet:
Power In from DC-DC converters
Power Out to DC-DC Converters
Aux. Servo Motor Interfaces
Power In, Current Sense, and Voltage Sense
Servo Motor Capactors
Neopixel LED Strip Interfaces
SPI Iinterface
Servo Motor Interfaces
UART Interface
Battery Connector
Contact Switches and LEDs
I2C Interfaces
Extra Power Connections
Microcontroller

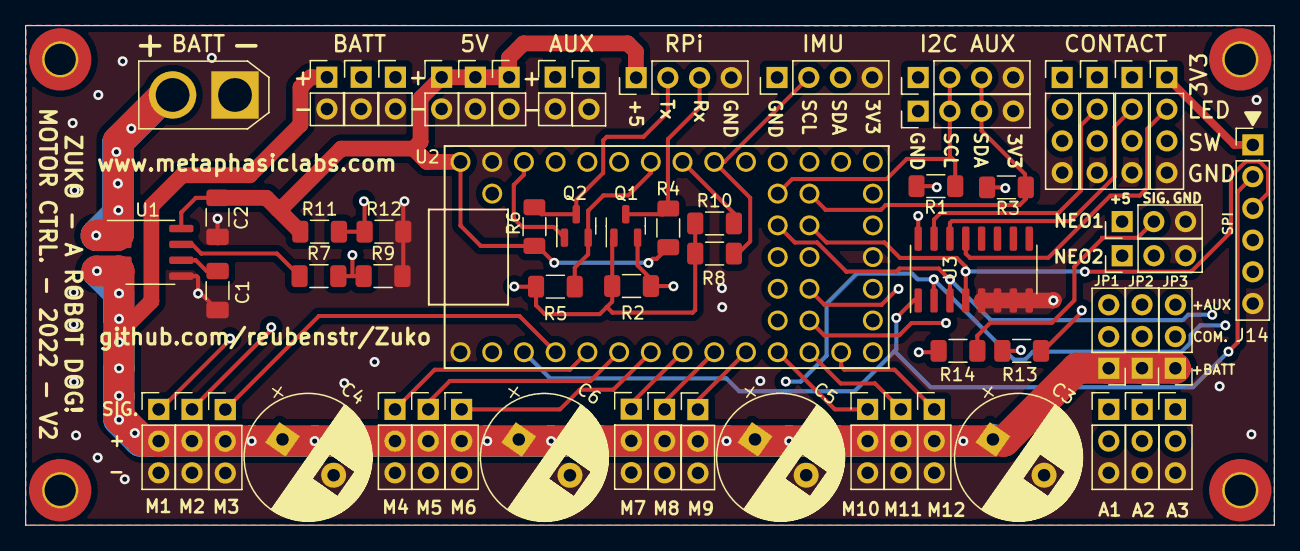
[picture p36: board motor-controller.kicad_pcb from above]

Board: 4 copper layers, 100.0 x 40.0 mm, 63 parts (0 on the bottom side), 52 nets.

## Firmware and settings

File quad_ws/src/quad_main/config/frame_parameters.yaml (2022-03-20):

# Frame parameters for Zuko v2.2
# Units in meters.

# x distance from hip pivot x-axis to perpendicular upper leg pivot y-axis
shoulder_length: 0.03175

# upper leg length from upper pivot point to lower pivot point
upper_leg_length: 0.100

# lower leg length from upper pivot point to foot ground contact point
lower_leg_length: 0.11225

# x distance between front and back upper legs pivot points 
hip_x: 0.238

# y distance between left and right upper legs pivot points 
hip_y: 0.091 #0.1545 

# x distance between front and back feet centers at ground touch 
foot_x: 0.238

# y distance between left and right feet centers at ground touch 
# foot_y: 0.169 
foot_y: 0.1545 # adjustment to have feet directly below hips (hips orientate to zero degrees when standing)

# how high center of body is off the ground
height: 0.195

# foot under upper leg servo offset (due to upper leg servos being shifted back in the CAD)
com_offset: 0.0105

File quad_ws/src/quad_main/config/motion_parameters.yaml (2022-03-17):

# Motion parameters and motion input limits
# Derived by trial and error for stability and physical limit breach prevention

lateral_fraction: 0.0
step_velocity: 0.001
swing_period: 0.200
clearance_height: 0.045
penetration_depth: 0.003

orn_x_min: -0.393
orn_x_max: 0.393
orn_y_min: -0.393
orn_y_max: 0.393
orn_z_min: -0.393
orn_z_max: 0.393

pos_x_min: -0.100
pos_x_max: 0.100
pos_y_min: -0.100
pos_y_max: 0.100
pos_z_min: -0.125 
pos_z_max: 0.070

yaw_rate_min: -0.785
yaw_rate_max:  0.785

step_length_min: -0.100
step_length_max: 0.100

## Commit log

2021-06-21 kinematics started
2021-09-13 CAD update.
    [_ROBO_FRONT_FRAME.DXF]
2022-01-15 file reorg
    [_ROBO_FRONT_FRAME.DXF]
2022-01-17 added CAD archive
2022-01-21 v2 kicad schematic and pcb started
    [zuko-teensy-motor-controller.kicad_pcb, zuko-teensy-motor-controller.kicad_sch]
2022-01-21 pcb update
    [zuko-teensy-motor-controller.kicad_pcb, zuko-teensy-motor-controller.kicad_sch]
2022-01-22 pcb progress
2022-01-24 pcb update - 2 layers to 4 layers
    [zuko-teensy-motor-controller.kicad_pcb, zuko-teensy-motor-controller.kicad_sch]
2022-01-25 update notes
    [zuko-teensy-motor-controller.kicad_sch]
2022-02-03 review file upload
    [zuko-teensy-motor-controller.kicad_pcb]
2022-02-05 battery board kicad version started
    [battery-board.kicad_pcb, battery-board.kicad_sch, battery-board.step]
2022-02-05 pcb update and project rename
    [battery-board.kicad_pcb, battery-board.kicad_sch, battery-board.step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]
2022-02-07 cad archive backup
2022-02-08 BOM format change
    [hardware-bom.ods]
2022-02-08 bom update
    [bom.ods, hardware-bom.ods]
2022-02-10 v2.1 frame started
    [battery-board.kicad_pcb, bom.ods]
2022-02-13 v2.1 update cad files
    [bom.ods]
2022-02-14 rpi4 expansion board creation
    [bom.ods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]
2022-02-14 expansion-board update
    [expansion-board.kicad_pcb, expansion-board.kicad_sch]
2022-02-14 expansion board update
    [expansion-board-pcb-outline.dxf, expansion-board-user-guides.dxf, expansion-board.kicad_pcb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]
2022-02-16 cad upload
2022-02-23 minor expansion board fixes
    [expansion-board.kicad_pcb]
2022-02-26 update CAD and BOM
    [bom.ods]
2022-02-27 Delete firmware directory
    Teensy 4.0 firmware directory moved to the old ROS2 with micro-ros workspace: https://github.com/reubenstr/micro_ros_quad_ws
2022-02-27 docs reorg
    [bom.ods]
2022-03-01 expansion board v1.0 release
    [expansion-board-B_Cu.gbr, expansion-board-B_Mask.gbr, expansion-board-B_Silkscreen.gbr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]
2022-03-05 frame v2.2 upload / file reorg
    [_ROBO_FRONT_FRAME.DXF, bom.ods, tool - press - bearing with horn into bridge v7.stl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]
2022-03-05 CAD tweak / BOM update
    [bom.ods]
2022-03-05 CAD update, lower leg angle fix to 45 degree offset
2022-03-06 upload quad_ws
    [BACK.stl, BATTERY.stl, Back.stl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]
2022-03-06 doc update
    [accessories.urdf.xacro, spot_accessories.urdf]
2022-03-08 zuko URDF first time in sim gym
    [bridge_back.stl, bridge_front.stl, butt.stl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]
2022-03-08 urdf update
    [zuko.urdf, zuko.urdf.xacro]
2022-03-11 frame param update / doc update
    [zuko.urdf, zuko.urdf.xacro]
2022-03-12 added joy index to gamepad as param
    [Back.stl, Back_Bracket.stl, Battery.stl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]
2022-03-13 moved quad_urdf into quad_simulation
    [BACK.stl, BATTERY.stl, Back.stl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]
2022-03-14 added joint index to hardware pin map
    [servo_parameters.yaml]
2022-03-14 removed unneeded mesh collisions in URDF
    [zuko.urdf, zuko.urdf.xacro]
2022-03-17 minor CAD tweak for better printing
    [BACK.stl, Front.stl, print-times-and-weights.ods]
2022-03-18 brought back quad_urdf into separate package for seperation of concerns
    [battery_cover.stl, bridge_back.stl, bridge_front.stl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]
2022-03-19 v2.2 STL upload, doc update
    [electronics - battery cover.stl, electronics - electronics mount .stl, electronics - main switch mounting.stl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]
2022-03-19 quad_motor bug fix
    [servo_parameters.yaml]
2022-03-19 motor calib file updated
    [servo_parameters.yaml]
2022-03-20 updates to joy interpt, frame param
2022-03-20 servo calibration script update
    [servo_parameters.yaml]
